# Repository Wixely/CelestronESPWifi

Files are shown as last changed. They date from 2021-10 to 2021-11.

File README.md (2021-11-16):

# CelestronESPWifi
ESP8266 based wifi adapter for Celestron telescopes

The official Celestron Skyportal WiFi module is €190~. (aka SkyQ Link, aka Skylink)

CelestronESPWifi parts list:
  * ESP8266 Module: €1.25c
  * Buck Converter: €0.75c
  * Cable: €3.00
  * Jellybeans: €2.00

Total = less than €10 anyway.

## Notes and Features ##

1. Confirmed working with Celestron SkyPortal App and Skysafari 6 Pro (Select scope type: "Celestron Wi-Fi").
2. Works with keypad (Tested on Celestron 4SE), not tested with other peripherals.
3. ESP firmware can be updated remotely over webpage via http.

## Example Build ##

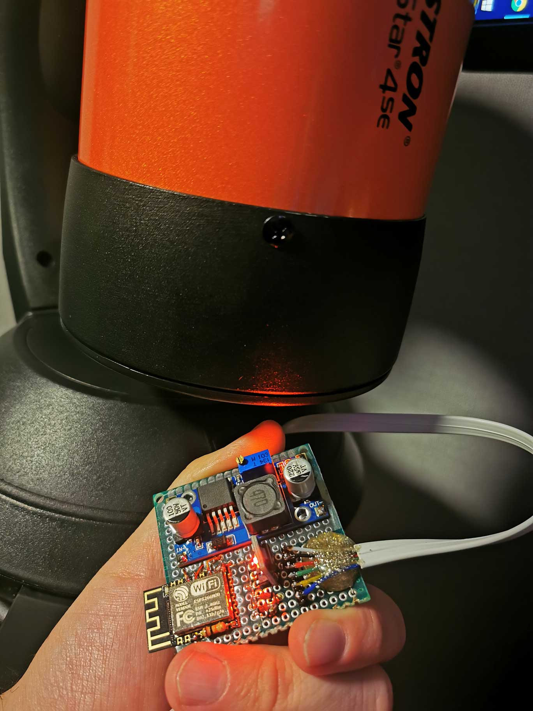
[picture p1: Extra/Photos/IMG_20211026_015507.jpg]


## Minimum Parts List ##

* ESP8266 Module (Example 12F)*
* ESP8266 Programmer*
* 2 Diodes
* 1 10K Resistor*
* Buck Converter (Example: LM2596)
* RJ12 Cable

*Alternatively you can use something like a NodeMCU and set the buck converter to 5v instead of 3.3v needed for a bare ESP.

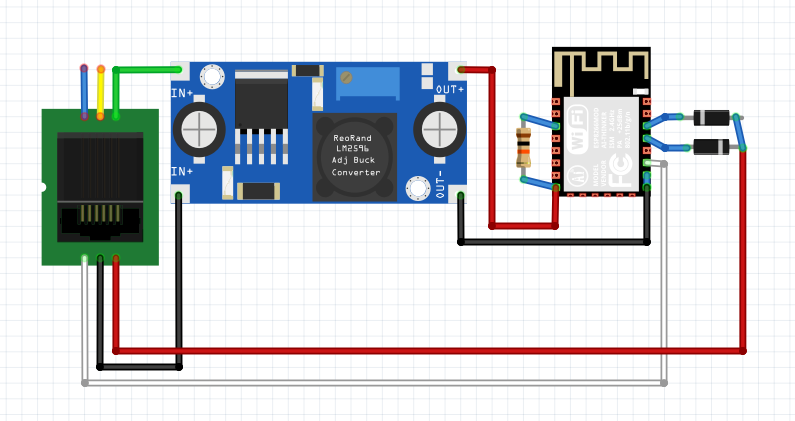
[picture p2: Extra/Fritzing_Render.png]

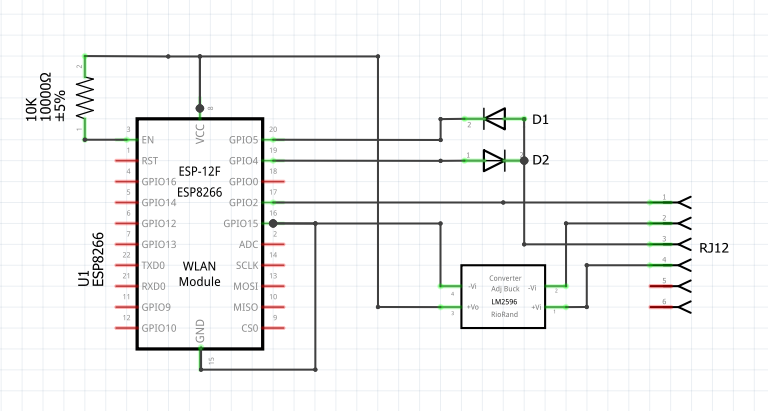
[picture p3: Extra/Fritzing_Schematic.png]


## Firmware Notes ##

ESP firmware will host a wifi access point, default named Celestron. The ESPs IP is 1.2.3.4 and opens a tcp listen port on port 2000. Don't change these as it's a requirement for the SkyPortal app to work. Port 80 can be accessed to update firmware over HTTP if required - please make sure to flash it before you embed it in a project :)

Because [SoftwareSerial](https://www.arduino.cc/en/Reference/softwareSerial) is used - we can choose what pins to TX and RX on, so if it needs changing afterwards this can be updated in the sketch and uploaded over HTTP. Just make sure the diodes are in the correct direction for the TX and RX data flow. Similarly the RST pin can be changed. If you plan to use a bare ESP, I recommend not to use GPIO15 as it will be shorted to ground.

## Hardware Notes ##

If you use a bare ESP; set the buck converter voltage to 3.3v, any other module such as a NodeMCU will take 5v.
The scope uses a UART system over one wire. Multiple devices can communicate on this same bus by pulling RST low, then sending data. Source and Destination IDs are sent in the packets so devices know what data is for them.
There have been varying reports from other smarter people on pull up/down resistor anomalies so if you deviate from this design you may come into those issues, see reading material below. If using a NodeMCU or other similar premade board, the pullup resistor and short on the EN pin and GPIO 15 are not needed. Be aware there are RJ12 cables with reversed colour layout, use a multimeter to find the 12v pin if you are unsure if you have a reversed version.

## Similar projects ##

This project would be much more difficult without the help of these posts:

https://sebastianfoerster86.wordpress.com/2020/08/10/celestron-teleskop-skyq-link-wi-fi-hack/

https://sites.google.com/site/wayneholder/nexstar-direct-telescope-mount-control

https://www.cloudynights.com/topic/652569-nexremote-cable-with-usb-ttl-serial-uart-converter-cable-with-ftdi-chip/page-2

Simply having this info meant that I could confirm my setup worked and my logic analyser was reading expected data.

## Additional Notes ##

On AA battery power, when the batteries are low at some point the motors will stop working. In this situation the ESP will probably still have power and the ability to communicate and link to the Skyportal app successfully. Input commands to the motor will not work, there is no indication of low power. It seems this behaviour is normal and even the official keypad gives you no low-power warning. Don't panic, simply get new batteries.

CelestronESPWifi was developed and confirmed working on a Celestron Nexstar 4SE.

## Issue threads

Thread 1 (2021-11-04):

Nexstar keypad and AP mode

5a796d, 2021-11-04:
Tested on nodemcu v3, unfortunately at the moment I don't have the telescope yet but the module is detected on the skyportal app in direct connect mode, I was wondering if it will also work in access point mode (without a telescope it is not possible for me to test it) and if in the future there will be a way to be able to use it even with nexstar keypad connected even if from what I have read around, the nexstar keypad does not work even with the original wifi module.

Thanks for the project!

Wixely, 2021-11-04:
Hi, thanks for the feedback! The code could be converted to connect to a wifi AP easily but I forsee serveral issues in practice as I haven't been able to get it to work on a very quick test:
1. If you wanted to use a phone hotspot, you would not be able to use the host phone with the App as not only are the wifi clients firewalled from the phone, the phone app will not consider you connected to a wifi AP and complain.
2. Celestion Wifi adapter needs to sit on 1.2.3.4 to recieve data - so the challenge here is that other devices connected to a normal AP will be on a different subnet by default (192.168.x.x). Solutions to this exist but it may not be convenient: (a) change the whole subnet of all the devices on the router, (b) set up some advanced rules for ip forwarding if you have a suitable router / pfsense.

As for the keypad issue I probably won't be investing too much time into solving this issue as I don't really need it myself. I understand some people prefer to use it when doing things like aligning and looking through the lens. You could try adding a physical switch to disable the TX/RX/RST lines for when you need the keypad? Maybe keep the RX line connected so the App gets feedback on changing position - I don't know if it will work.

5a796d, 2021-11-05:
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

For the AP mode that's just what I was interested in knowing, I'll do some tests! As for the keyboard it was just a matter of comfort as you specified but it is not strictly essential.

Thanks!

5a796d, 2021-11-05:
One last question, the pull up resistor on nodemcu I have the doubt that it should be connected on vcc (5v) or on 3v3 pin

Wixely, 2021-11-05:
>certain buck modules of dubious quality

Thanks for your advice, I know the XL6009 boost converters famously have a flaws if the voltage drops too low but I wasn't aware of the buck converter problems. I do always give a quick test on modules before I use them.

> One last question, the pull up resistor on nodemcu I have the doubt that it should be connected on vcc (5v) or on 3v3 pin

If you're talking about the resistor I have in the diagram connecting EN pin to 3v3 for the ESP module - you don't need this in a NodeMCU. Without this resistor the bare ESP will not turn on at all, but inside the NodeMCU board it already has everything it needs to boot up once it gets 5v.

5a796d, 2021-11-05:
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

The diode is just a small protection in case of problems with the buck / step down module, it is not strictly necessary but it is an extra safety, in case of a burn the module does not return to the telescope any overvoltage

Here's why my nodemcu worked even without pull ups, thanks for the tip

5a796d, 2021-11-07:
gpio15 on nodemcu has 10k pull down, do I still have to connect the gpio15 pin to gnd?

Wixely, 2021-11-08:
Hi @5a796d, no again that is only required for the bare ESP and it will not boot up without it. The NodeMCU does not require it.

Wixely, 2021-11-08:
@5a796d I don't know what to say really, maybe I never correctly tested this before - but the keypad is working fine for me with the ESP plugged in. I can even move the keypad and watch it update on the SkyPortal app in realtime. I haven't made any changes to hardware or code but either one of two things has happened: I had assumed it didnt work because of an earlier version of my build and  just assumed it would never work, or something inside the scope changes to break this randomly as [Sebastian alluded to in his experiments](https://sebastianfoerster86.wordpress.com/2020/08/10/celestron-teleskop-skyq-link-wi-fi-hack/).

Translated:
> It was strange: if the ESP8266 was connected without the NPN collector circuit, the RX pin of the ESP8266 could not be driven to GND at all times, as if a very strong (1k?) Pull-up was occasionally switched on at the RX pin of the ESP.

5a796d, 2021-11-11:
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

Something is not right about your scheme and that of sebastianfoerster86 that you linked, apparently the connections to the aux port seem different and I don't understand why, could you elucidate me just to understand? Thank you

P.S.
I am still without a telescope but if you can I would do a test to see if by powering the pin select as per sebastianfoerster86 diagram the keypad remains operational or just does not want to know that it works

Wixely, 2021-11-12:
Hi @5a796d, indeed I'm aware that his diagram is different from mine as it was one of the stumbling blocks I had along the way. If you check the other link from wayneholder you can see that [his diagram](https://sites.google.com/site/wayneholder/nexstar-direct-telescope-mount-control/IMG_5661.JPG?attredirects=0) matches mine and that sebastian's appears to be mirrored relative to mine. Additionally if you see the [first page of the cloudynights forum post](https://www.cloudynights.com/topic/652569-nexremote-cable-with-usb-ttl-serial-uart-converter-cable-with-ftdi-chip/) that I linked in the readme, the user johnschnupp is espousing the same concerns you are. This confusion may also be compounded by the fact that RJ12 cables can come in reversed forms and it's possible I even developed it using one of these "bad" cables. I will try improve my diagram if I confirm this is the case.

For me, the way I identified which was the correct pinout was to use a multimeter to find the 12v pin, from that you can determine if you have the reversed version or not. The RST (Select) pin will then be the pin farthest away from that. The TX and RX pins are on each side of the 12v, they are also shorted to each other inside the scope so you can confirm this by using a multimeter in continuity mode on the wires each side of the identified 12v wire. The GND is then the only unidentified pin between all of the identified pins (CST will be opposite side of RST). If you use batteries, the 12v pin can appear as low as 10v sometimes but no other pin is anywhere near this high. During development I tried a lot of different things but in nearly every case the keypad showed an Error 17, thats why I was so convinced that it was broken.

5a796d, 2021-11-12:
I understood. thanks for the explanation, the problem of the cable I do not ask myself because I build it, I only had doubts about the connection because the diagrams are different in the connection to the aux port.

thanks again, as soon as the telescope arrives I will test it

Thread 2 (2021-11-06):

NexStar 6SE not responding

joeldhenry, 2021-11-06:
Hi, Thanks so much for your project! Perfect timing as I just got a 6SE and am looking to remote control it. i've Done the exact setup you have, except using a WEMOS D1 mini. I flashed the code onto the MCU and connect to it on my phone with the Skyportal App, However when I click connect i get a timeout of 3x "TCP:  3B 03 20 10 FE CF" and the app says the telescope isn't responding. Ive setup the variables as:

int RTSPin = 2 (GPIO2 -> Select)
int UartTXPin = 4 (GPIO4 -> Serial Send)
int UartRXPin = 5 (GPIO5 -> Serial Receive)

i know the RX & TX are the right way (same as your diagram).

Any Ideas?

Wixely, 2021-11-06:
I don't have a Wemos to try but from Google I can see they are using Aarduino pin naming scheme. I do know that pins 2 and 4 are mixed up when using arduino notation on esp so D2 = GPIO4 and D4 = GPIO2 so my first suspicion is that. I would try using different pins from 5 onward as they should match up OK. If you attach the keypad and monitor via serial on the Wemos you should see data from the keypad (hit buttons), that will at least diagnose if the scope is communicating at all.

joeldhenry, 2021-11-07:
ive changed to:

int RTSPin = D4;
int UartTXPin = D2;
int UartRXPin = D1;

When I have the keypad attached & power on with ESP plugged into aux port I get "No Response 16". I've tripple checked the schematic and tested connections and everything matches.

Wixely, 2021-11-08:
You have to be aware that Pin 2 (gpio2) is not D2 and Pin 4 (gpio4) is not D4 and in the case of the wemos specifically, Pin 5 (gpio5) is not D5. Please make sure you are using GPIO pin layout and not the "D" notation layout.

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

If you still have issues then for a test I would disconnect the ESP TX and RST completely and connect the RX pin (plus GND and 3v3). With the RX only connected you should see data from the keypad in serial monitor assuming you have the pins correct  - you may still need the diode for this but it might work without it.

You say it's in the Aux port so thats correct. I remember seeing posts online about the the other ports having a reversed pin layout on some scopes so be aware.
Also I will point out that I commonly saw "Error 17" on they keypad often during development but I've never seen "Error 16". Google says these are references to each motor inside - interesting that your scope tries to communicate with 16 instead of 17 first but they effectively seem like the same problem and it would be due to pulling one of the wires high or low incorrectly.

joeldhenry, 2021-11-09:
Yea i get an Error 16. i give up, too scared of blowing up the scope haha. glad it works for you!

Wixely, 2021-11-09:
>i cant replicate with my Nexstar 6SE

That's a shame, there is always the chance there is some kind of different between our scopes and I understand completely about being cautious. It could be that your wemos is also a factor, possible that it has a defect or that it doesnt quite work exactly as my setup. You can see from the images folder that I [developed it using a generic esp programmer](https://github.com/Wixely/CelestronESPWifi/raw/main/Extra/Photos/IMG_20211025_165345.jpg) (very similar to NodeMCU). The other thing I wonder is that maybe our cables our different? Patch cables and crossover cables exist for RJ12 so possible the colours don't match up to the same pins. And after checking the [cable I bought] and used for the project (https://www.amazon.co.uk/gp/product/B07BHNWV28) it appears lots of people in the comments are complaining about it being a crossover cable with the pins reversed!

joeldhenry, 2021-11-17:
i have 2 thoughts, either its the cable pinouts from the nexstar, or its the firmware of the mount/controller.

A couple of things to note, you didn't mention in your schematic the actual pins and rotation of the telescope aux port, this would be really helpful for debugging. Also your diagram and sketch code do not match, you have GPIO5 as receiving and GPIO4 as transmitting, but use 4 are receiving and 5 as transmitting in your sketch. i know you mentioned this in my issue, but this was not in the original readme

joeldhenry, 2021-11-17:
I think i uncovered the issue! the NexStar 6SE/8SE has seperate RX & TX Pins rather than the single serial pin your example shows.

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

joeldhenry, 2021-11-17:
looking at at the diagrams. Arduino RTS -> -CTS_AUX3, Arduino TX -> RX_AUX3 are correct, but we also need Arduino RX <- TX . Which explains why i'm not receiving anything from the telescope. Plus your code says Pin5 is TX and Pin4 is RX which are backwards to the schematic.

Wixely, 2021-11-17:
>Plus your code says Pin5 is TX and Pin4 is RX which are backwards to the schematic.
Hi @joeldhenry Thanks for noticing that indeed you are correct, I'll try get this updated later today.
>NexStar 6SE/8SE has seperate RX & TX Pins
Can you test this with a multimeter to see if they are indeed seperate, my 4SE has the TX and RX has seperate pins but they are shorted, these pins are each side of the 12v pin. This info would be good to add.
>A couple of things to note, you didn't mention in your schematic the actual pins and rotation of the telescope aux port, this would be really helpful for debugging.
I think this is a good idea, will try to write up something soon.
Your diagram looks completely different in layout to my pins, where did you find this? I might need write a more generic approach to acommodate different scopes.

joeldhenry, 2021-11-17:
thanks so much! i think very close to figuring out what is wrong with my setup! the diagram i got was from https://www.cloudynights.com/topic/576390-looking-for-8se-aux-labelled-pinout/, ill confirm if my pins are shorted too, i suspect you are correct and they are. I also found this document http://www.paquettefamily.ca/nexstar/NexStar_AUX_Commands_10.pdf which page 11 has a pinout. This document has heaps of information about how the scope communicates too if you are interested!

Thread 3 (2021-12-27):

RJ12 Diagram has incorrect wiring (backwards).

rhass, 2021-12-27:
The wiring diagram shows pins 1-4 used on the RJ12 connector. This appears to be backwards. The correct pin for Vcc is on pin 3 and Ground is Pin 5.

Please note, I haven't got my scope to connect yet so I cannot confirm the correct pins for Rx/Tx -- but for sure these should be shifted to Pins 6 and 4.

rhass, 2021-12-27:
I found a forum post which appears to have the correct pinout for the connector.

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

https://www.cloudynights.com/topic/652569-nexremote-cable-with-usb-ttl-serial-uart-converter-cable-with-ftdi-chip/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

5a796d, 2022-01-17:
I confirm that the rj45 connection is the other way around.

in your diagram you have inserted 1n4001 between esp and step down which is useless except to cause you to have a voltage drop, the diode in question should already be present on the pin vin of your esp board, it is advisable that you mount a 1n5817 / 18/19 between rj45 and step down to protect the telescope

Wixely, 2022-01-17:
Regarding the RJ12 connector, I'm unhappy with my diagram and I plan to redo it. One of the issues is that the RJ12 cables come in reversed versions, and I think I've been using a reversed cable. Thank you very much for your input.

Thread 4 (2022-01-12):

Controls problem

icefabio, 2022-01-12:
I made your project with a wemos d1 mini which compared to the original scheme I only removed the resistance.

It works but from SkyPortal or SkySafari the up / down / right / left controls that move the telescope do not work well. Sometimes they get stuck or stay in motion.

I was having a doubt. Could it be the diodes? I have mounted some IN4148. They are correct?

Thank you!

Note I have a Celestron Nexstar 5 STL

5a796d, 2022-01-17:
i don't know d1 mini, try unplug GPIO15 from GND.
GPIO15 should already be connected to GND on the board via pull down resistor.

should there be no changes try to reverse tx and rx on the code, it is in the first lines

Wixely, 2022-01-17:
Hi @icefabio, I have seen this happen too during development. If you unplug your telescopes keypad do you see an improvement? It could be the RTS pin (GPIO2) is not working correctly. Keep in mind that GPIO2 is marked as D4 on the Wemos D1 Mini. Similarly GPIO4 is marked as D2. If you have these mixed up then it might behave as you describe. Can you check the pins are correct?
I think your diodes should be fine if you are able to get the scope to move at all, if they arent correct then you most likely wouldnt be able to connect in the first place.

icefabio, 2022-01-17:
Hi, many thanks for you reply :)

> i don't know d1 mini, try unplug GPIO15 from GND. GPIO15 should already be connected to GND on the board via pull down resistor.

My wemos doesn't have G15 connected to GND.

icefabio, 2022-01-17:
Hi @Wixely,

> Hi @icefabio, I have seen this happen too during development. If you unplug your telescopes keypad do you see an improvement?

No, same problem. :(

> It could be the RTS pin (GPIO2) is not working correctly. Keep in mind that GPIO2 is marked as D4 on the Wemos D1 Mini. Similarly GPIO4 is marked as D2. If you have these mixed up then it might behave as you describe. Can you check the pins are correct?

Yes. RTS is correctly connected to G2 (D4 in my board).

This is my complete scheme:

<a href='https://postimg.cc/9rTFQfMW' target='_blank'>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</a>

I also tried to make a circuit exactly like yours with a 12F but the problem is the same. :(

F

icefabio, 2022-01-20:
Hi @Wixely, just to be sure .. which type of diode did you use?

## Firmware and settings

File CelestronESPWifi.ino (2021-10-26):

#include <ESP8266WiFi.h>
#include <WiFiClient.h>
#include "SoftwareSerial.h"
#include "WebServer.h"

/* Variables you can change */
const String ssid = "Celestron";
const String pw = "Celestron";

int RTSPin = 2;
int UartTXPin = 5;
int UartRXPin = 4;

/* Variables you should NOT change */
IPAddress hostIP(1, 2, 3, 4);
IPAddress subnetMask(255, 255, 255, 0);
WiFiServer tcpServer(2000);
SoftwareSerial serialTX;
SoftwareSerial serialRX;
WiFiClient tcpClient;
byte buffer[1024];
byte bufferByte;
int bufferSize = 0;

void setup() {
  pinMode(RTSPin, OUTPUT);
  digitalWrite(RTSPin, HIGH);
  delay(100);
  Serial.begin(19200);
  Serial.println("Starting");
  serialTX.begin(19200, SWSERIAL_8N1, UartTXPin, UartTXPin, false, 256); 
  serialRX.begin(19200, SWSERIAL_8N1, UartRXPin, UartRXPin, false, 256); 
  serialTX.enableIntTx(false);
  serialRX.enableIntTx(false);
  serialTX.enableTx(true);
  serialRX.enableTx(false);
  
  WiFi.mode(WIFI_AP);
  WiFi.softAPConfig(hostIP, hostIP, subnetMask);
  WiFi.softAP(ssid, pw);
  StartupHostHTTPServer();
  
  tcpServer.begin();
  delay(100);
}

void loop() {
  while(!tcpClient.connected())
  {
    tcpClient = tcpServer.available();
    server.handleClient();
    //delay(10);
  }

  if (TransmitData(&tcpClient, &serialTX)) //send data from tcp client to scope
    delay(2); 

  TransmitData(&serialRX, &tcpClient); //send data from scope to tcp client
}

int TransmitData(WiFiClient* tcp, SoftwareSerial* uart)
{
  int sentData = 0;
  if (tcp->available())
  {
    Serial.print("TCP: ");
    while (tcp->available())
    {
      bufferByte = (byte)tcp->read(); // read the data and pipe it directly to the scope uart
      Serial.print(bufferByte < 0x10 ? PSTR(" 0") : PSTR(" "));
      Serial.print(bufferByte, HEX);
      buffer[bufferSize++] = bufferByte;
    }

    digitalWrite(RTSPin, LOW);
    uart->write(buffer, bufferSize);
    uart->flush();
    digitalWrite(RTSPin, HIGH);
    
    bufferSize = 0;
    sentData = 1;
    Serial.println();
  }
  return sentData;
}

int TransmitData(SoftwareSerial* uart, WiFiClient* tcp)
{
  int sentData = 0;
  if (uart->available())
  {
    Serial.print("UART: ");
    while (uart->available())
    {
      bufferByte = (byte)uart->read(); // read the data and pipe it directly to the tcp client
      Serial.print(bufferByte < 0x10 ? PSTR(" 0") : PSTR(" "));
      Serial.print(bufferByte, HEX);
      buffer[bufferSize++] = bufferByte;
    }
    tcp->write(buffer, bufferSize);
    bufferSize = 0;
    sentData = 1;
    Serial.println();
  }
  return sentData;
}
